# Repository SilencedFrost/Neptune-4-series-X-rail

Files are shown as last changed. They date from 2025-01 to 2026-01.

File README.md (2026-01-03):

# Neptune 4 series X rail

Shield: [][cc-by-nc-sa]

This work is licensed under a
[Creative Commons Attribution-NonCommercial-ShareAlike 4.0 International License][cc-by-nc-sa].

[][cc-by-nc-sa]

[cc-by-nc-sa]: http://creativecommons.org/licenses/by-nc-sa/4.0/
[cc-by-nc-sa-image]: https://licensebuttons.net/l/by-nc-sa/4.0/88x31.png
[cc-by-nc-sa-shield]: https://img.shields.io/badge/License-CC%20BY--NC--SA%204.0-lightgrey.svg

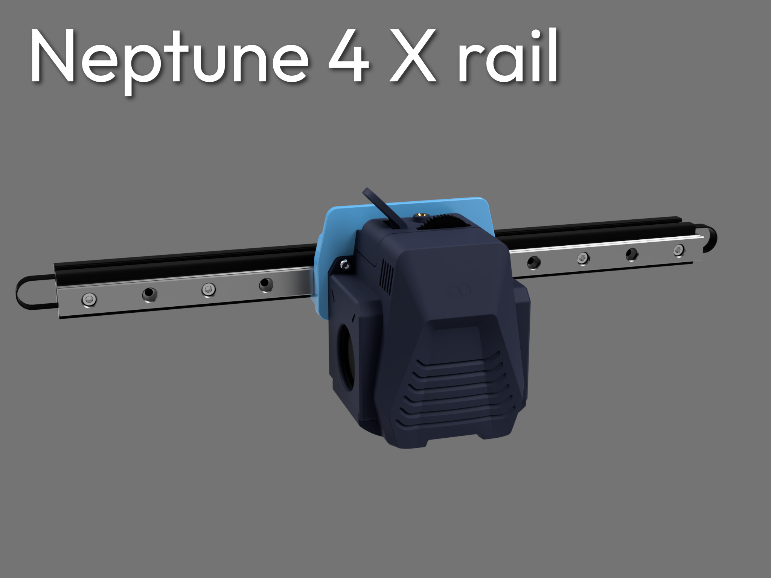
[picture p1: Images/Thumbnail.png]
Thumbnail


## Introduction

The design allows you to put a front mounted MGN12H linear rail on the neptune 4 series.

Many testing data yielded from 20% to 75% increase in recommended accel via input shaping(IS), with a reduction in vibrations and corner smoothing measured via a nozzle adxl.

### Features
- Improved COM placement.
- Increased rigidity.
- Proper parallel belt path.
- Increase movement accuracy, toolhead rigidity.
- Lowers the gantry compared to toolhead -> z cable bracket no longer hitting tie rods.
- Retains most mod compatibility (cable chains, fan mods, etc).
### Cons:
- 8mm loss in Y axis compared to stock.
- Renders the aux fan null.
- Requires skill, hardware, and machine tuning.

🤩 Do you like the design? You can help fund innovations like this!

[Consider supporting me!](https://buymeacoffee.com/silencedfrost)

Much appreciation given to my supporters, and you get exclusive access to various CAD files!

Submit feature requests [here!](https://trello.com/b/vacGVoLQ/cad-modelling-requests)

## BOM (Only listing extra parts, no stock)

I'll get a commission if you shop here!

[SF-Affiliate-landing-page](https://silencedfrostaff.carrd.co/)

|Item |Amount|Recommended source |
|---|---|---|
|MGN12H linear rail |1 |Youmetong MGN12H_z2 / BSTMotion stainless MGN12H_z2 |
|EU profile 2020 extrusion |1 | |
|Gates gt2/edpm gt2 6mm belt  |1 |Mellow |
|Lithium grease | |Mobilux EP2/Mobil XHP222 |
|Filament | |PETG-GF/CF or ABS/ASA and above |
|M3x35mm BHCS |2 | |
|M3x40mm BHCS |2 | |
|M3x16mm BHCS |4 | |
|M3x6mm FHCS |4 | |
|M3x10mm FHCS |1 | |
|M3 Hex/Square nut |4 | |
|M4x8 BHCS |4 | |
|M4 T-nuts |4 | |
|M3x8mm SHCS |plenty| |
|M3 T-nuts |plenty| |
|M3 heat inserts (<4.7mm OD)  |4 | |
|10mm metal drillbit |1 | |
|6900-2rs |1 | |

### Rail, extrusion, and belt lengths

|Model |Rail |Extrusion |Belt  |
|---|---|---|---|
|Base/pro|295mm-325mm|355mm |820mm |
|Plus |400mm-430mm|460mm |1040mm|
|Max |480mm-510mm|540mm |1200mm|

### Note: get highest preload option the brand offers for budget rails

## Print settings

STL wasn't accounted for shrinkage, compensate as needed.

### Minimum:
- 3 walls.
- 1 mm top-bottom.
### Recommended
- 5 walls.
- 1.6mm top-bottom.
- 0.2mm layer height.

# Assembly guide

## Inserting heatsets

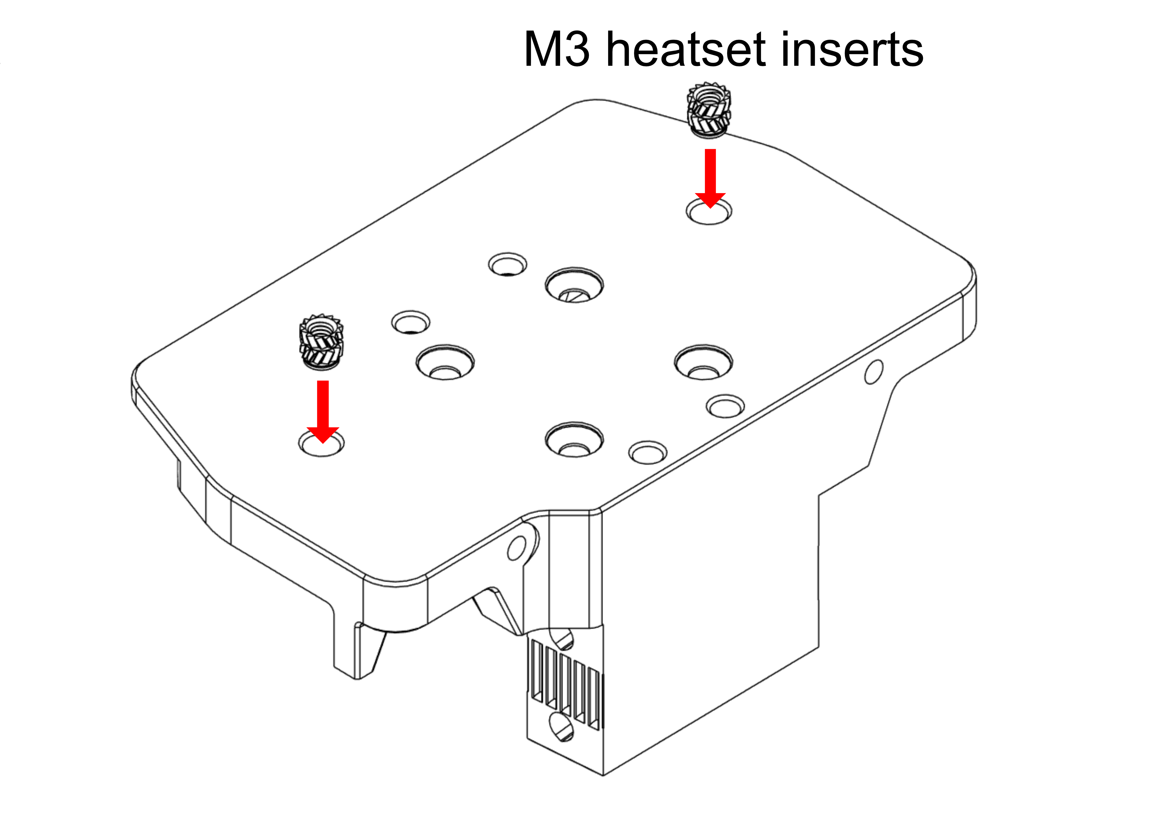
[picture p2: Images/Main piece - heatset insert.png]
Insert 2 into main piece


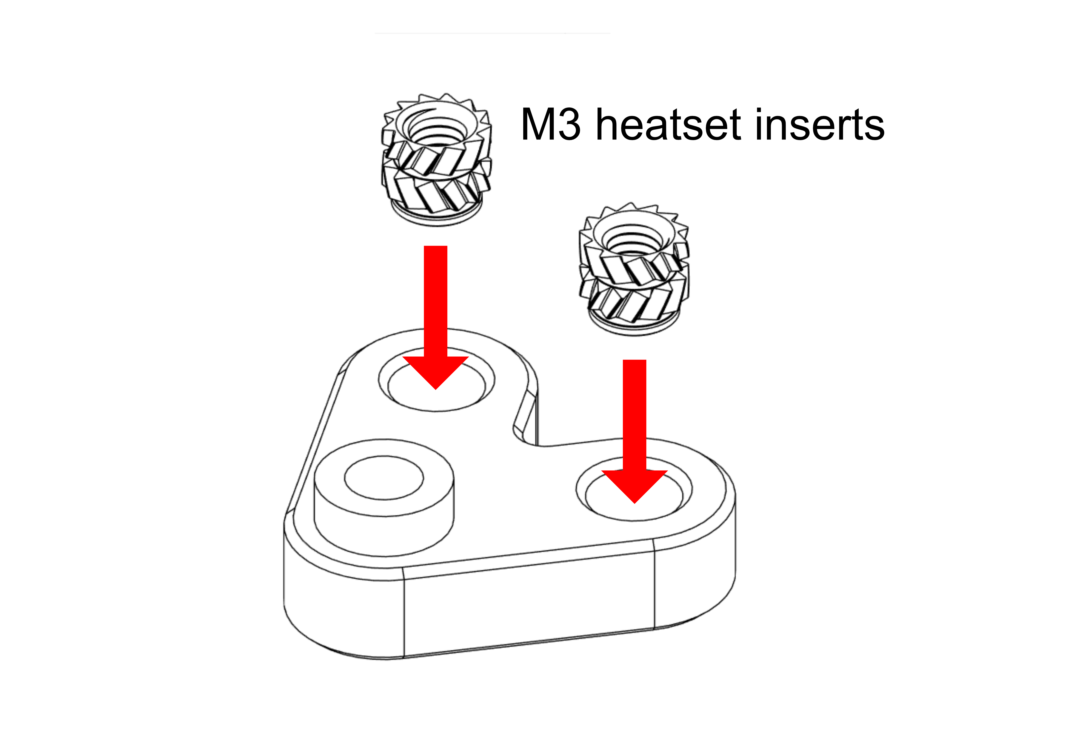
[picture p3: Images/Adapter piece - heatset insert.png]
Insert 2 into adapter piece


## Drilling extrusion x2 (One hole for each end)

### Assembling drill guide tool

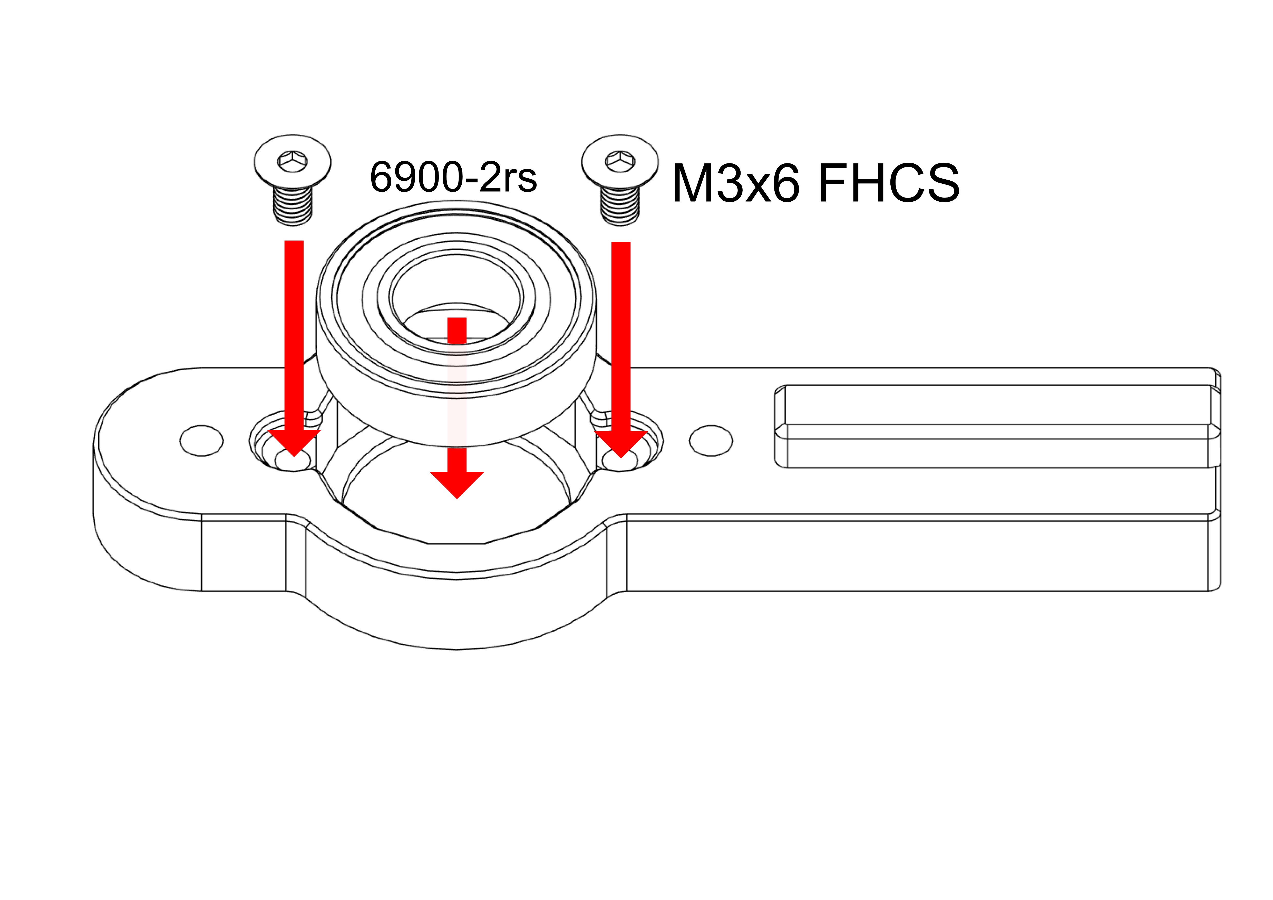
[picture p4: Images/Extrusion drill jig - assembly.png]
Assembling drill guide


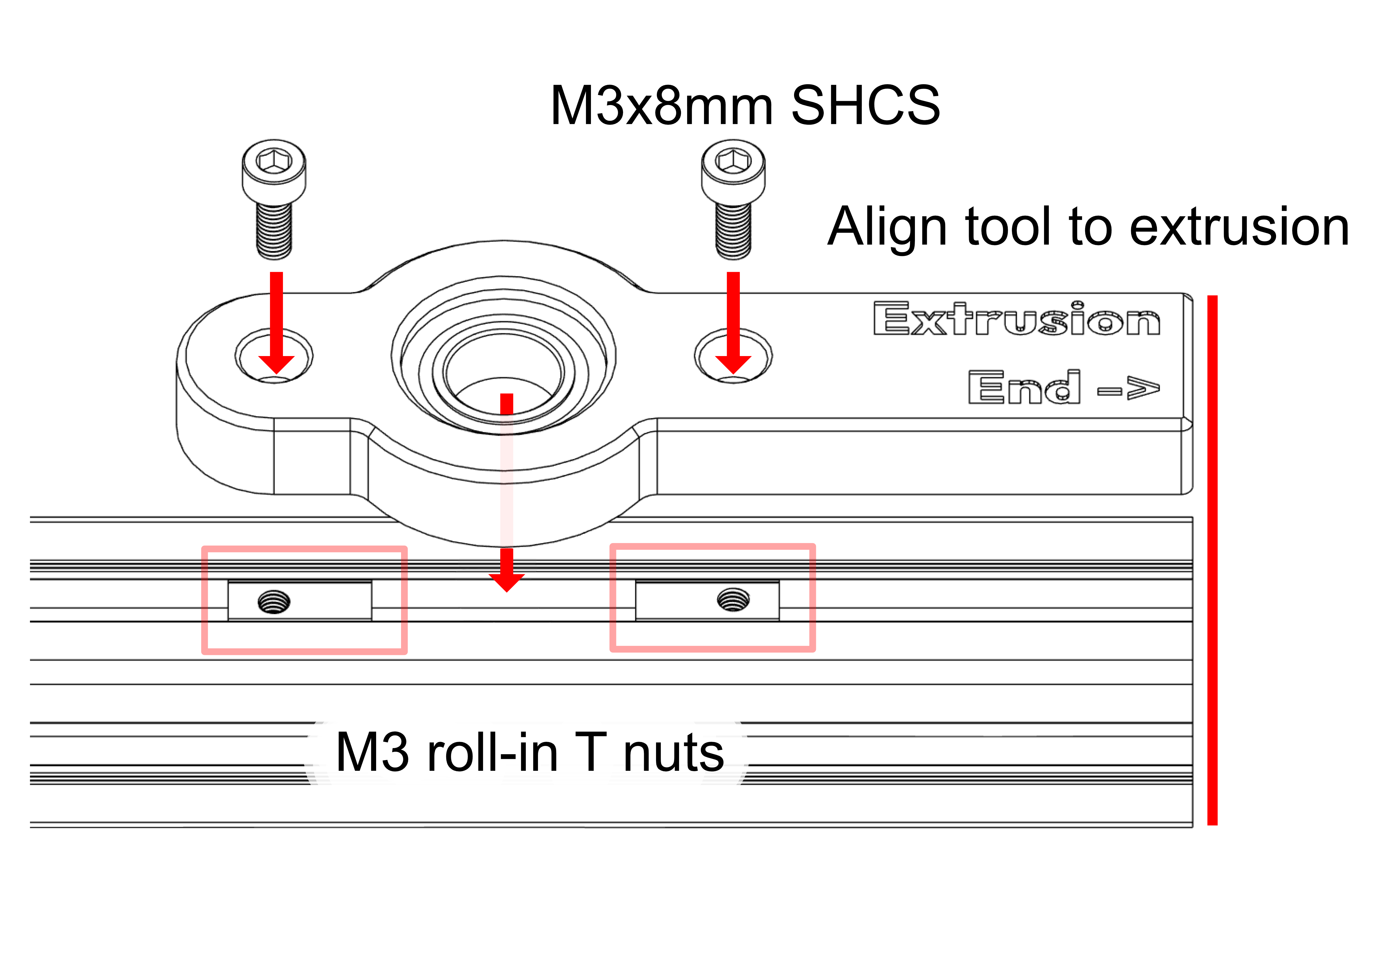
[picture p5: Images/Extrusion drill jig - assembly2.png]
Putting drill guide on


### Drilling the extrusion

Run at high rpm and feed the drillbit in slowly, or else it'll bite on the aluminum and you'll have a bad time! Hold the extrusion down tight.

There's no need to drill deeper than the first top flange.

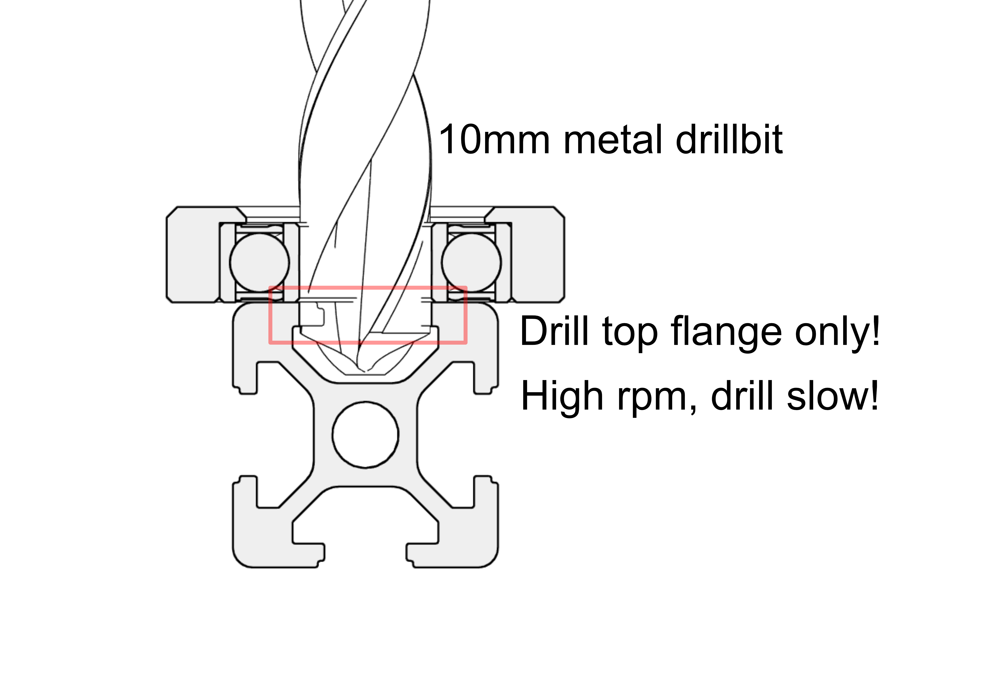
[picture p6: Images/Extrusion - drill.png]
Drilling extrusion


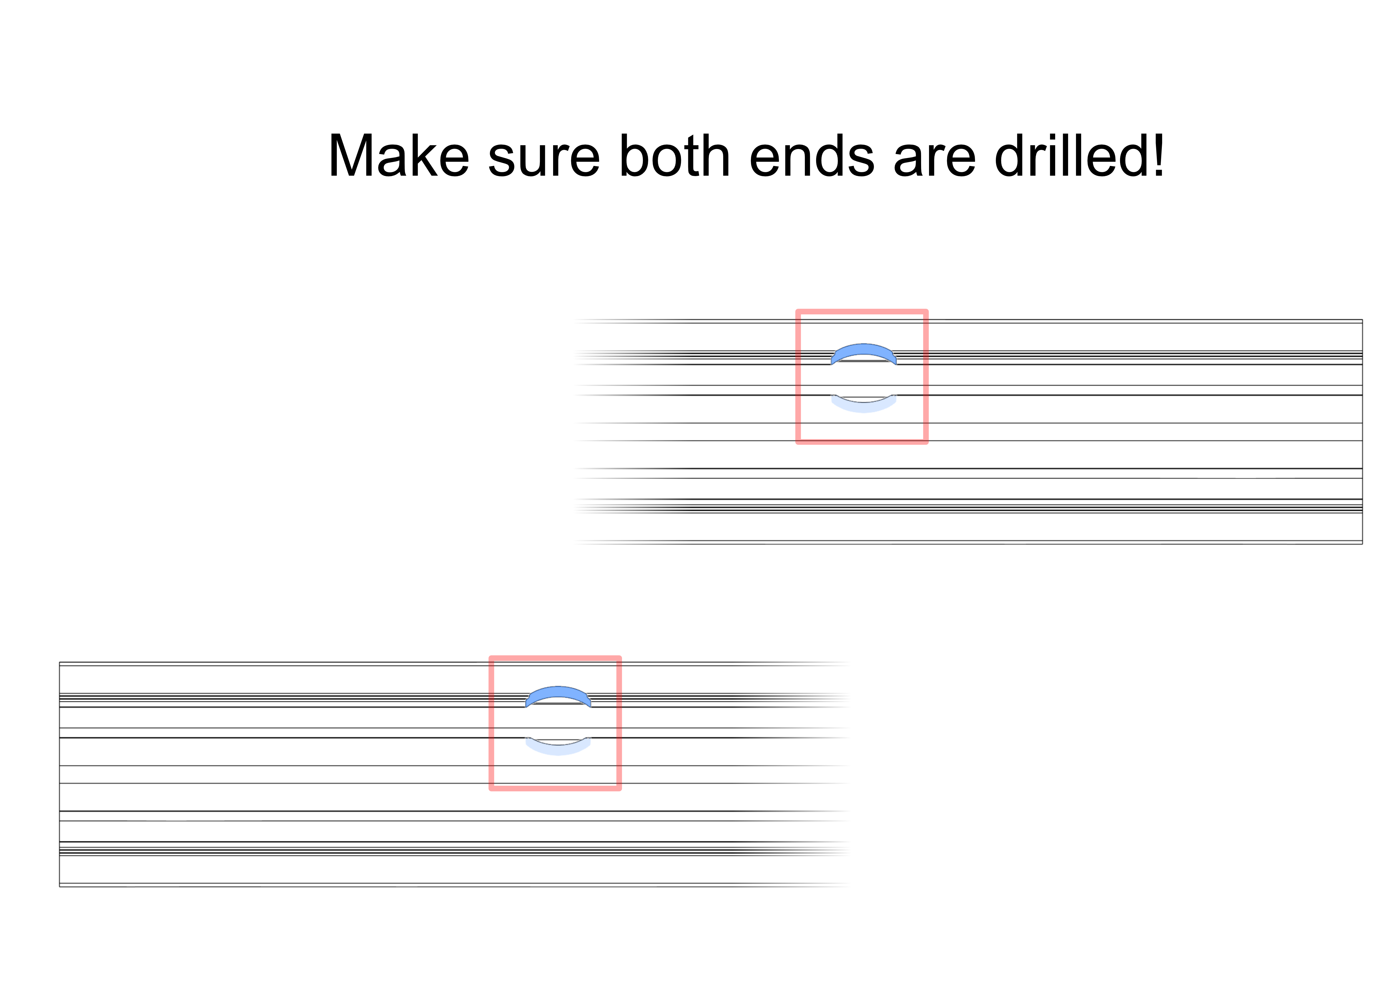
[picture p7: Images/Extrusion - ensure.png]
Ensure both ends drilled


## Mounting the rail

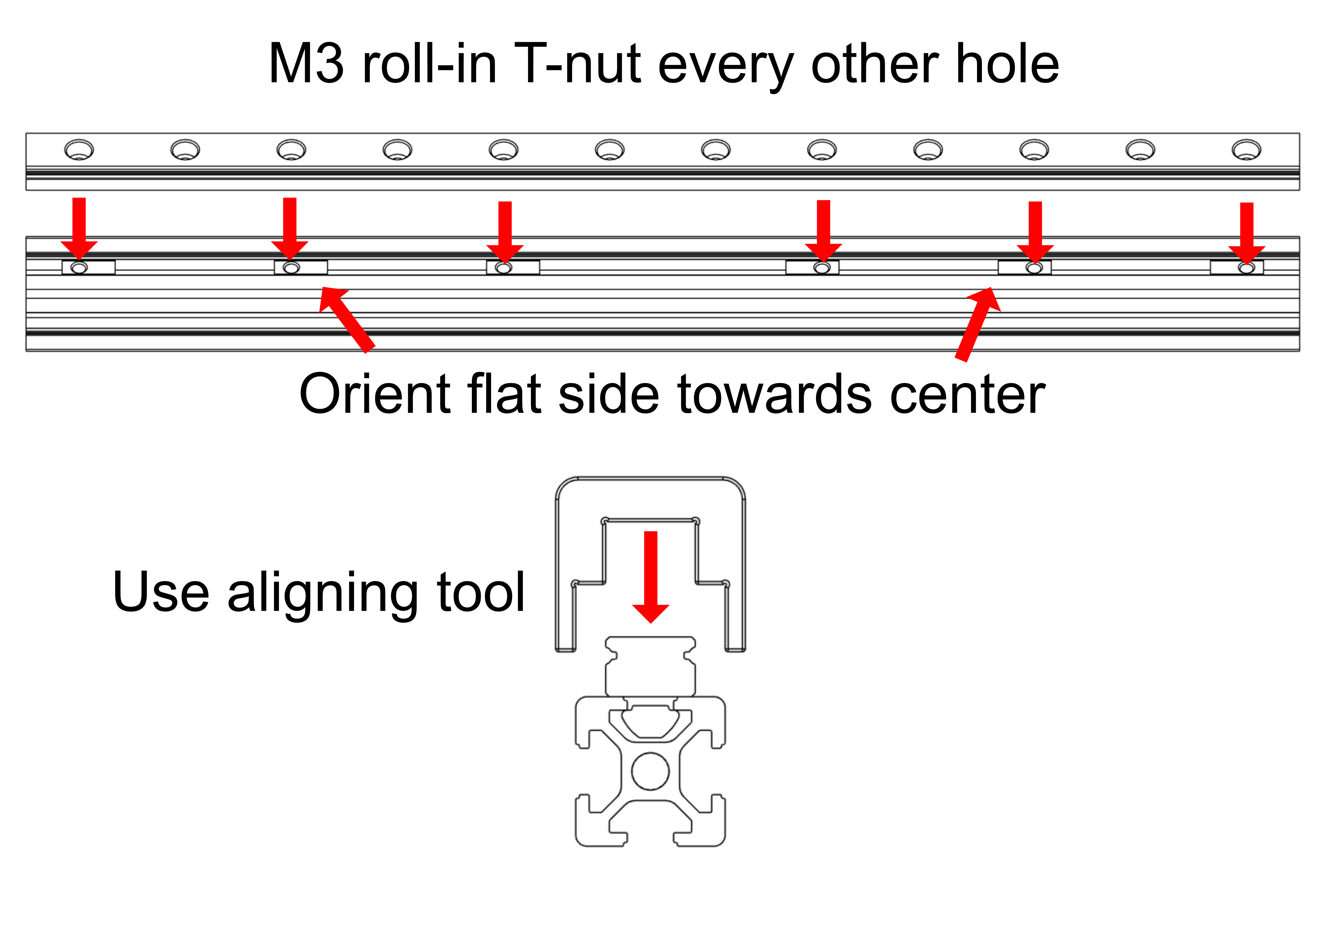
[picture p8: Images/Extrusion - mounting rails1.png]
TNuts and Alignment


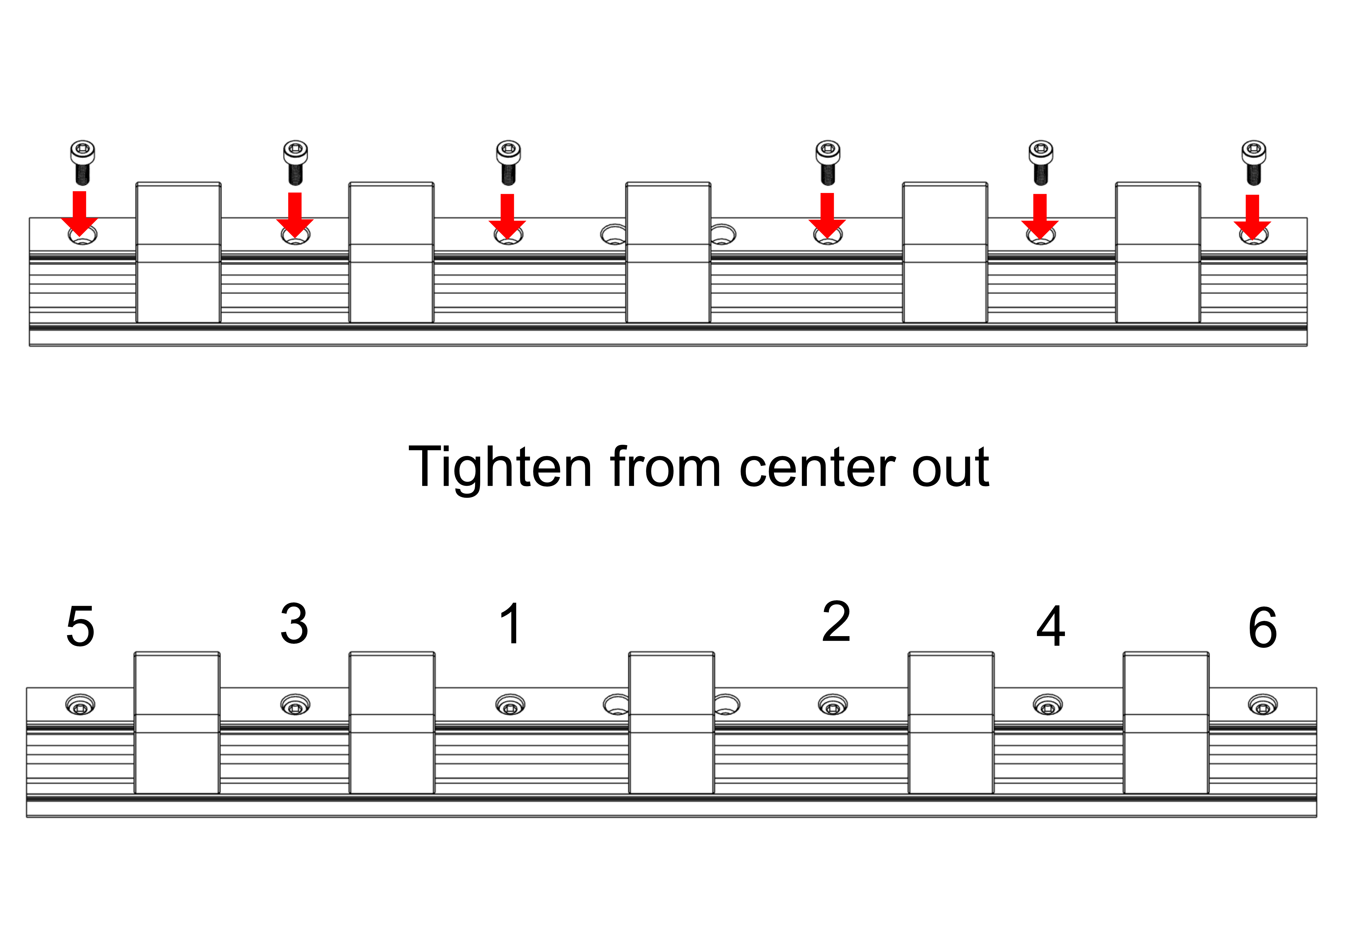
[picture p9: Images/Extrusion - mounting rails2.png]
Screwing down


## Disassembling stock gantry

### Taking out the gantry

Take off the toolhead + cabling

Remove the top brackets, bar, and z belt + pulleys

Pull the X gantry out the top

### Disassembling stock gantry

Remove 2 endcap covers

Remove the X belt

Undo 4 M4 screws holding the brackets to the beam

Remove the M3 TNut on the new beam (from the drill jig)

Insert 4 M4 TNuts corresponding to where the bracket holes are

## Assembling the new gantry

### Putting on the beam

Loosely screw on the brackets with 4 M4x8 BHCS

Put the assembly back onto the z extrusions

Tram the gantry, adjust eccentric nuts

Tighten 3 out of the 4 accessible M4 screws

Take the gantry out again

Tighten the last M4 screw

Put the assembly back onto the z extrusions

Tram the gantry

Put back the z belts, top beam, top brackets, loosely screw the top brackets in place

Run the gantry to max height with synchonized z

Tighten the top brackets

Why all this you ask? you just perfectly trammed your gantry and made sure the z beams are parallel!

## Final assembly of the adapter

### Preparations

Install the MGN12H cart via 4 M3x6 FHCS

Insert 4 M3 Hex/Square nuts into the recesses of the belt clamp

Screw on the toolhead adapter onto the toolhead with M3x10mm FHCS

### Assembly

Slide the carriage onto the rail

Install the belt with the belt clamps with 4 M3x16mm BHCS

(Optional) Install Lamarc's chain with 2 M3x8mm FHCS

Install the toolhead

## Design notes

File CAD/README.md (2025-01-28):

# CAD files for Neptune 4 series X rail mod
Supporters can contact me to get latest nightly build CAD file

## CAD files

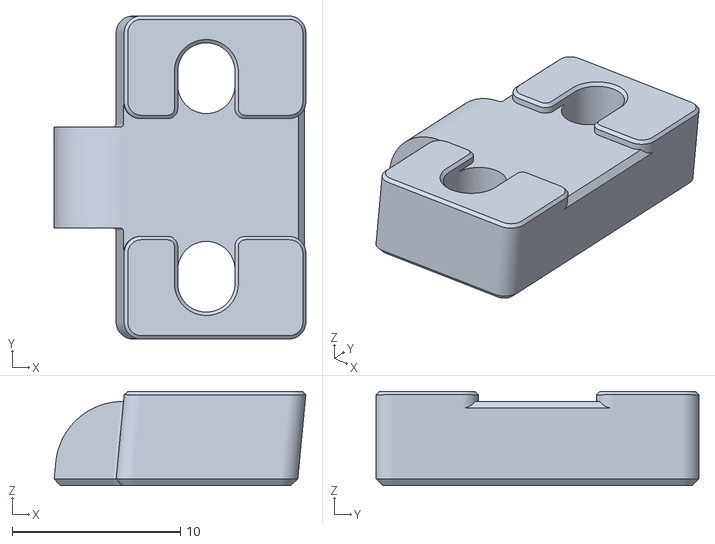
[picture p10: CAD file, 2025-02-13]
STLs/Bracket/Belt clamp_x2.stl
15.0 x 19.2 x 5.60

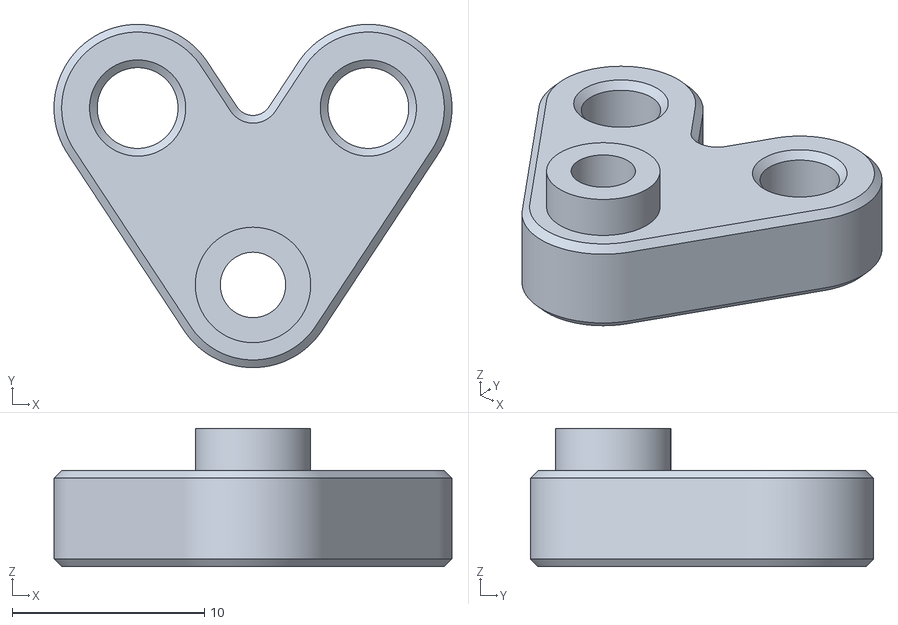
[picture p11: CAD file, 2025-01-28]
STLs/Bracket/Toolhead adapter.stl
20.7 x 17.8 x 7.20

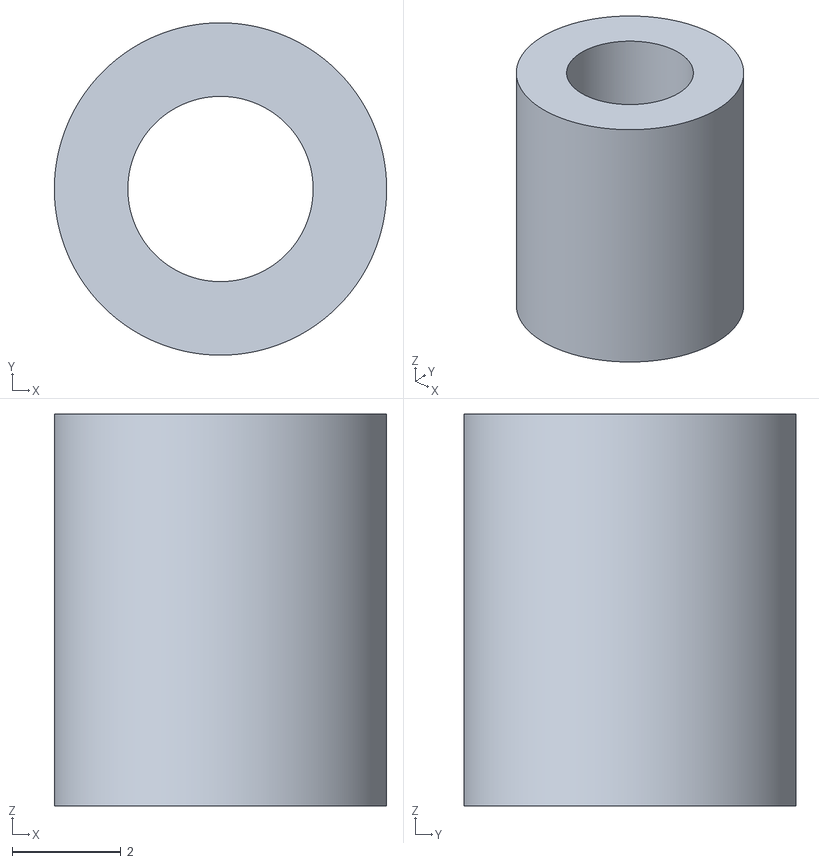
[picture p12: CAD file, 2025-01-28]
STLs/Bracket/Toolhead spacer_x2.stl
6.10 x 6.10 x 7.20

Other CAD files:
STLs/Tools/Hole drill jig.stl

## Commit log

2025-01-28 Re-exported and split stls, added README for CAD
    [Belt clamp_x2.stl, Toolhead adapter.stl, Toolhead spacer_x2.stl]
2025-01-28 adjusted drill jig to simplify bom
2025-01-28 updated drill jig to use M3x6FHCS to hold down bearing
2025-01-29 Corrected total width to 88mm
2025-01-31 added drill jig assembly picture
2025-01-31 added more extrusion prepping pictures
2025-01-31 updated extrusion drill jig - assembly2
2025-01-31 called out the drillbit size
2025-01-31 updated drill jig to use M3x8mm SHCS
2025-01-31 added extrusion-ensure
2025-01-31 modified jig to space bearing away from extrusion, prevent scratches
2025-02-01 added rail alignment jig stl
2025-02-01 Rename hole drill jig.stl to Hole drill jig.stl
    [Hole drill jig.stl]
2025-02-06 Added 40mm to belt length, for easier installation
2025-02-13 Added holes for Lamarc's chain, added anti-crush for belt clamps, tightened hex hole
    [Belt clamp_x2.stl]
2025-02-18 updated main bracket to have right endstop
2025-04-19 added steps to mount rail
2026-01-03 Clarified aluminum extrusion size in README

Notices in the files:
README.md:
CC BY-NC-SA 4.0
